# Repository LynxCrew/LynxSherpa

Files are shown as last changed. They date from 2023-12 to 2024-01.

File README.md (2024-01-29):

# LynxSherpa

## Caution: not thouroughly tested!
## CAUTION: Rn it seems as if the wear on the gears is quite high
I have to do some additional testion concerning this but rn I would not use it

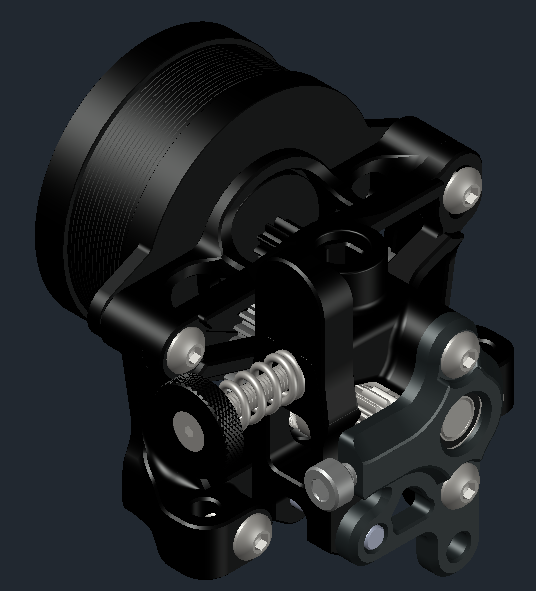
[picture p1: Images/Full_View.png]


## Why another Sherpa:
I was looking for a new extruder as my Orbiter started dying on me and had my eyes on the sherpa mini.
Doing a bit more research, I looked at the sailfin and found a mod keep the tensioner open for easier filament swaps which led to look for mods of the sherpa mini as well in my pursuit of finding the perfect extruder.
I stumbled across the Sherpa Zero and thought it looked promising, though it had 4 major drawbacks imo:
- It was not RIDGA compatible and my RIDGA gears were already on their way, so using RIDGA was set in stone
- Having the angle adjustment screw on the tensioning arm defeats it's whole purpose imo
- The bridge on the front housing just doesn't really look good when printed
- No way to add a bowden collet (well this carries over from the original sherpa mini)

That's where the LynxSherpa comes in:
The angle adjustment screw now sits in the front housing, the bridge is gone, the cad is cleaned up, it is RIDGA compatible and there is a core piece ready for a bowden collet (the small one that's used on the hextrudort or orbiter).
When adjusting the angle adjusment screw, make sure to leave a little play, you'd rather still have a little bit of wood grain than worn out gears.

## Workings:
The general idea is the same as with the Sherpa Zero, the adjustment screw is just fixed now instead of in the tensioning arm.
I would also advise to use a nylon screw to not damage the axle of the idler gear. <br>
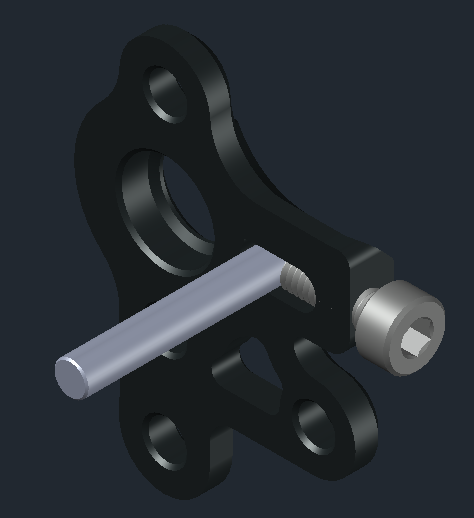
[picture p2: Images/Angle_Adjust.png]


## File names:
There are 2 different tensioning arms like with the original sherpa mini: a long and a short one.
There are also 2 version of the core: the default one (dubbed normal) and one which will accept a bowden collet (dubbed collet)
For the front housing there are 4 versions: a normal one and one for extruder mounts like on the armchair xol where you can add one screw from the front (dubbed XOL).
Both of those versions feature a version for a "long" angle adjustment screw (m3x8) or a short one (m3x6).
There is also a file for a printed version of the m5x7x0.5 shim.
The optional folder contains a Turbiter mod which fits the LynxSherpa (and the normal sherpa) on an Armchair XOL.

## Credits
[Sherpa Mini](https://github.com/Annex-Engineering/Sherpa_Mini-Extruder) <br>
[Sherpa Zero](https://github.com/jrlomas/Sherpa-Zero)

## Changelog

### v1-0-1
- adjusted the size of the printed shim to be a snug fit on the axle so it doesn't slide off on it's own when disassembling the extruder
- added a little groove in the face plate so it looks nicer
- added printable m3 shims, I used one on the m3x20 axle of the tensioning arm (facing the core) and 2 on the idler grae axle, one on each side (totally optional)

### v1-0-0
Initial release

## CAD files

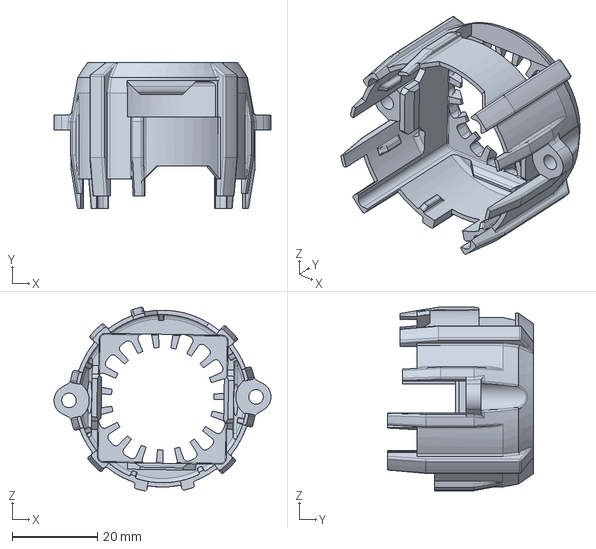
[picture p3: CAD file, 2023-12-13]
CAD/Turbiter_Sherpa_1-0-0.step
50.8 x 34.3 x 43.0 mm

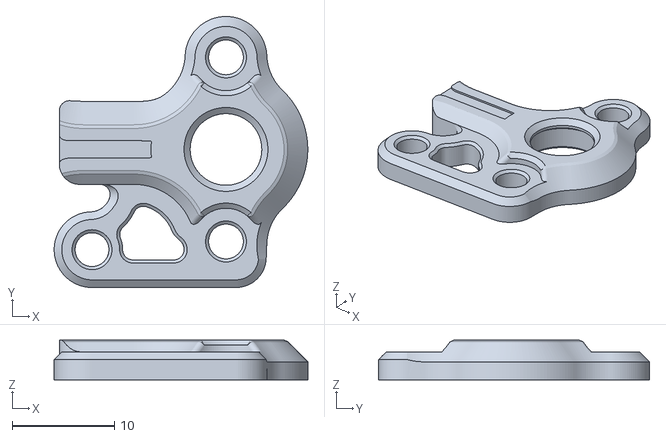
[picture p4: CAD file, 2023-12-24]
STLs/Tension Screw Left (Mirrored)/[a]_housing_front_normal_long_screw_x1.stl
24.8 x 26.5 x 3.90

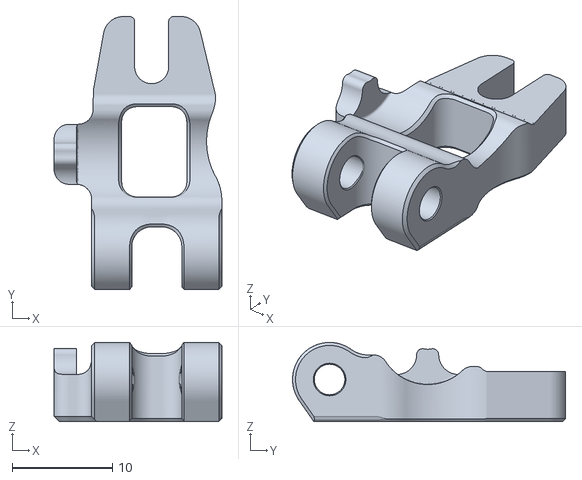
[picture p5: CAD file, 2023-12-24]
STLs/Tension Screw Right (Default)/idler_arm_short_x1.stl
16.8 x 27.3 x 7.90

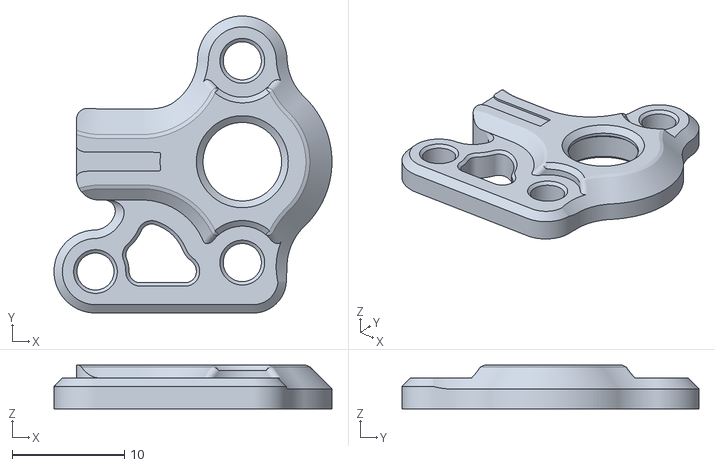
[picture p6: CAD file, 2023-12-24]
STLs/Tension Screw Left (Mirrored)/[a]_housing_front_normal_short_screw_x1.stl
24.8 x 26.5 x 3.90

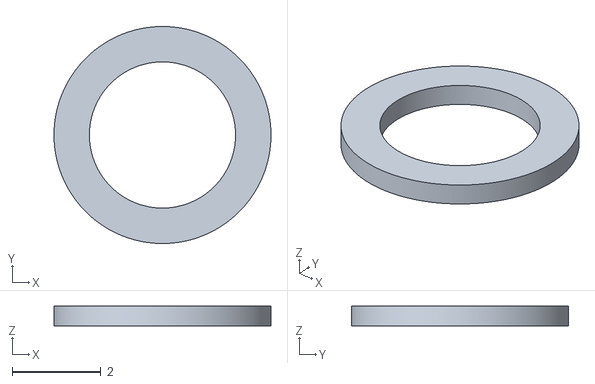
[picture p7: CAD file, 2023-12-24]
STLs/Tension Screw Right (Default)/printed_shim_m3.stl
4.90 x 4.90 x 0.45

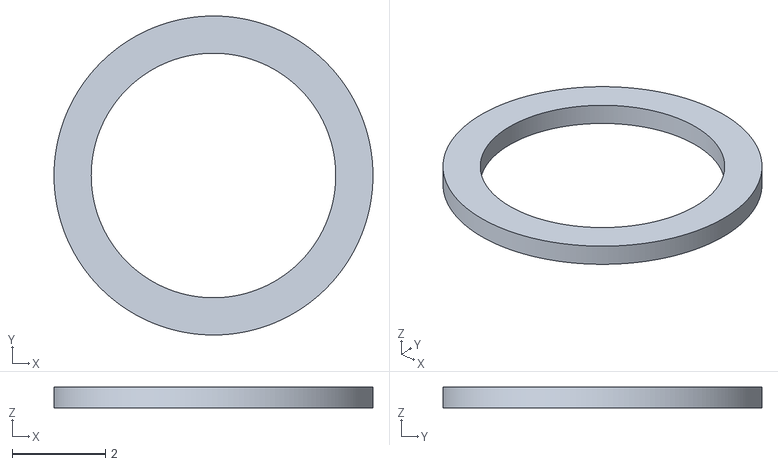
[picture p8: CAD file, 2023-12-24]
STLs/Tension Screw Left (Mirrored)/printed_shim_m5_x1.stl
6.85 x 6.85 x 0.45

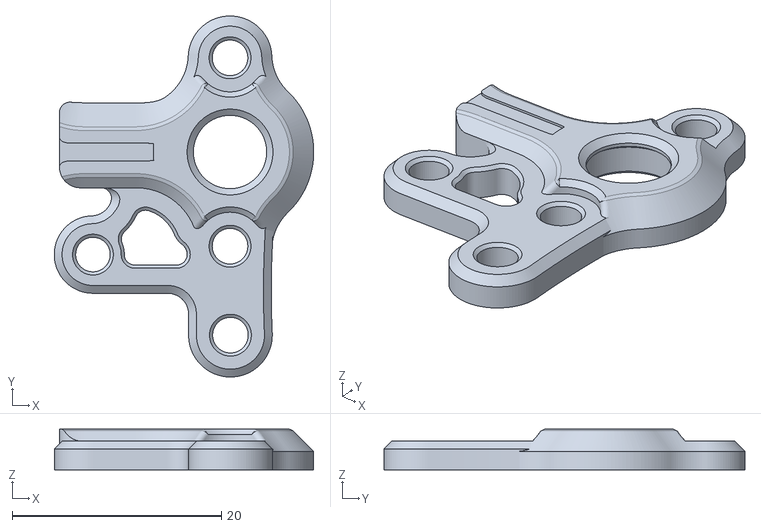
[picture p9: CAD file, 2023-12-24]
STLs/Tension Screw Left (Mirrored)/[a]_housing_front_xol_long_screw_x1.stl
24.8 x 34.5 x 3.90

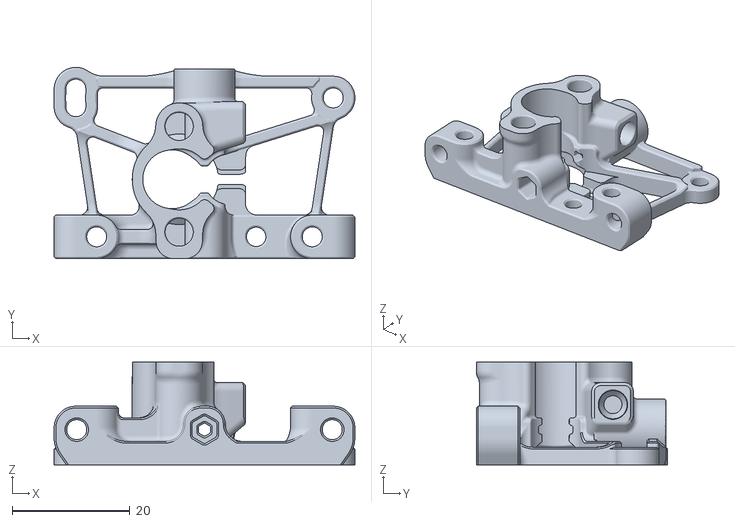
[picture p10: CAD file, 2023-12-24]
STLs/Tension Screw Right (Default)/housing_core_collet_x1.stl
51.2 x 32.5 x 17.5

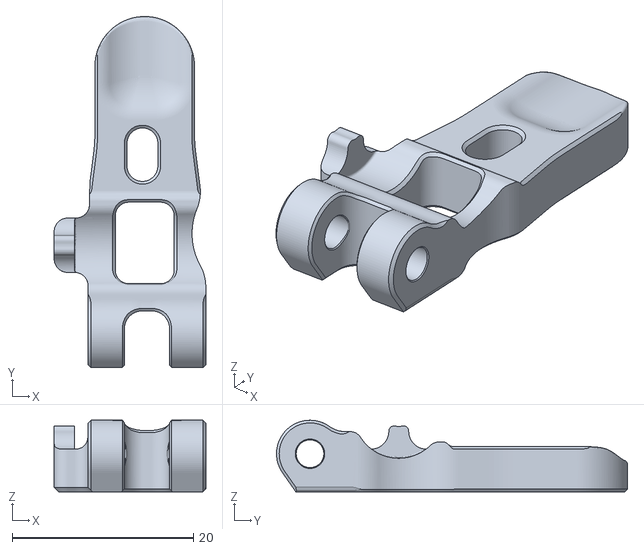
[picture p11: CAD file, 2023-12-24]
STLs/Tension Screw Right (Default)/idler_arm_long_x1.stl
16.8 x 38.8 x 7.90

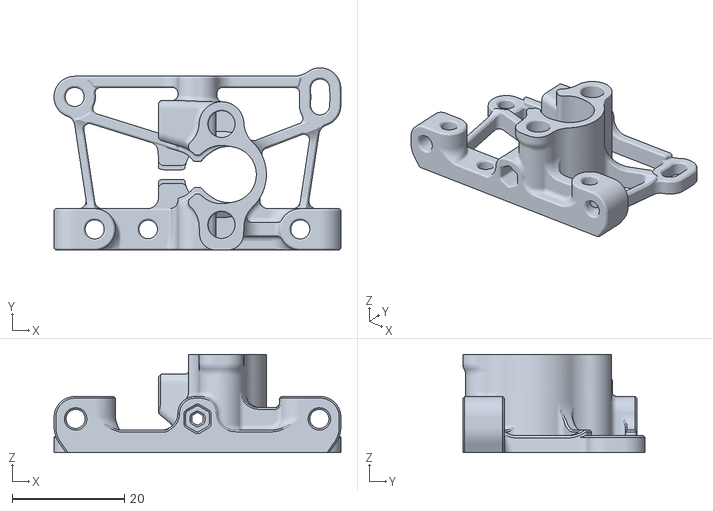
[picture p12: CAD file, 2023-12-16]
STLs/Tension Screw Left (Mirrored)/housing_core_x1.stl
51.2 x 32.5 x 17.5

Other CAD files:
STLs/Optional/Turbiter_Sherpa.stl
STLs/Tension Screw Right (Default)/[a]_housing_front_normal_long_screw_x1.stl
STLs/Tension Screw Left (Mirrored)/[a]_housing_front_xol_short_screw_x1.stl
STLs/Tension Screw Right (Default)/[a]_housing_front_normal_short_screw_x1.stl
STLs/Tension Screw Left (Mirrored)/housing_core_collet_x1.stl
STLs/Tension Screw Right (Default)/[a]_housing_front_xol_long_screw_x1.stl
STLs/Tension Screw Left (Mirrored)/housing_rear_x1.stl
STLs/Tension Screw Left (Mirrored)/idler_arm_long_x1.stl
STLs/Tension Screw Left (Mirrored)/idler_arm_short_x1.stl
STLs/Tension Screw Right (Default)/[a]_housing_front_xol_short_screw_x1.stl
STLs/Tension Screw Right (Default)/housing_core_x1.stl
STLs/Tension Screw Right (Default)/housing_rear_x1.stl
